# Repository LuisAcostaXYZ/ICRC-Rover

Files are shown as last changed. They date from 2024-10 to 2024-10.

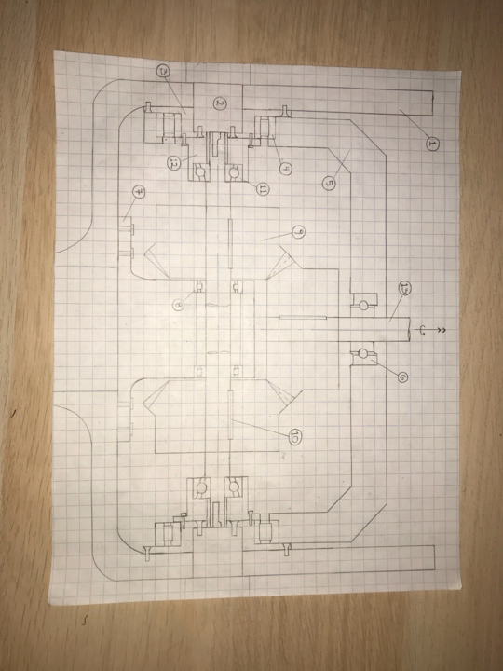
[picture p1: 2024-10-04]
3. ARM/3.0 2020-21 Arm/4. Robotic Arm/Robot 2.0 Design Files/Wrist/Wrist_2DSketch_v2.png

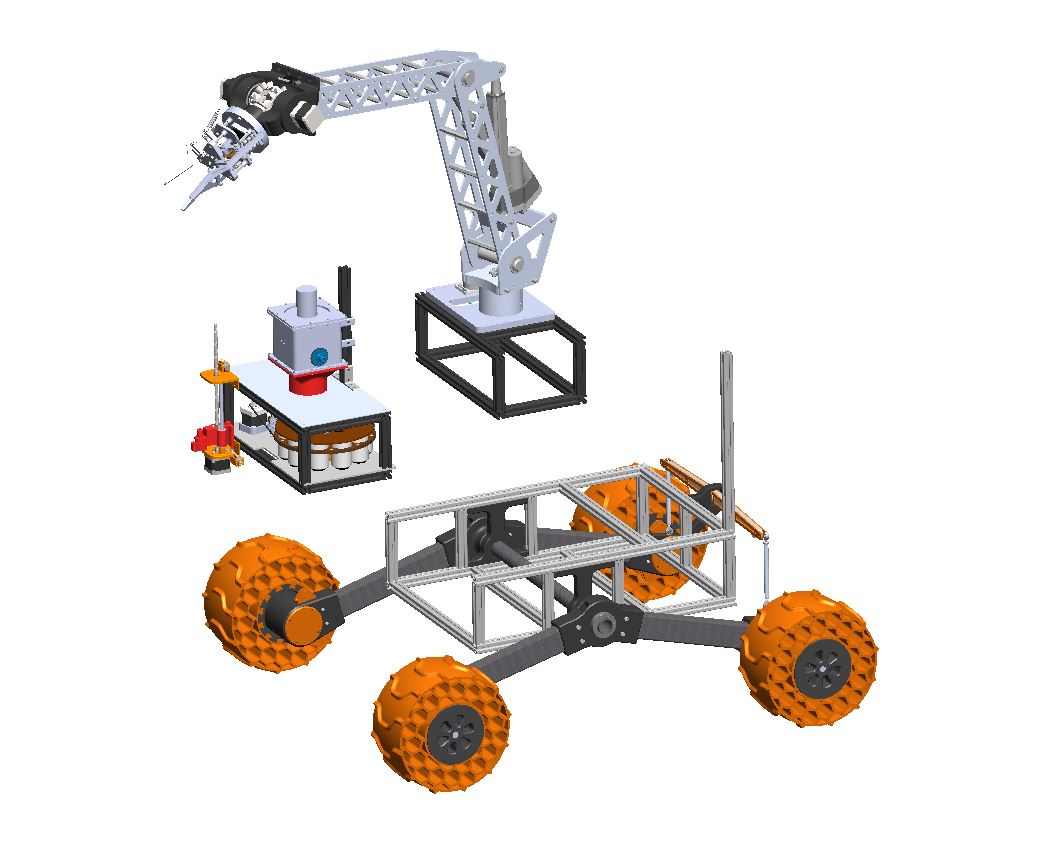
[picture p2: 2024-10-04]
Rover_thumbnail.JPG

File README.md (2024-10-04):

<h1>CIRC Rover</h1>

<h2>Description</h2>
The Canadian International Rover Challenge is a competition held every year in Drumheller, Alberta. This event brings together talented college and university STEM students from around the world. Here they have the chance to demonstrate their engineering abilities in robotic systems. The competition challenges the teams to design a space rover capable of overcoming difficult scenarios. These include traversing varying terrain, autonomous operations, and remote dexterity challenges using a robotic arm.
<br />

 ### [Video Demonstration](https://youtu.be/Zh-UuSO0Gxo?si=WTbHEEzv2XzP8nVz)
<p align="center">
UAV assembly
</p>

<h2>Software Used</h2>

- <b>SolidWorks</b> 

<h2>Directory structure:</h2>

The project is divided in 3 modules:  <br/>
- <b>1-CNC (Chassis and Suspension)</b>
- <b>2-LYF (Life Detection Dystem)</b>
- <b>3-ARM (Robotic arm)</b> <br/>

With an additional folder <b>"0-ROV"</b> containing the main assembly.

As the leader of the "Chassis and Suspension" division I supervised the progress the design, manufacturing and assembly of the models contained in the folder <b>“1-CNS”</b>.

<h2>ScreenShots:</h2>

<p align="center">
Chassis and suspension: <br/>
WingStructure
<br />
<br />
Wheel assembly:  <br/>
Wheel Assembly
<br />
<br />
Aluminium structure: <br/>
Aluminium structure
<br />

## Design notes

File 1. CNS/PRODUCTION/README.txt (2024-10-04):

All drawings and production documents are put here.

1. Create folder with the part number and name of the part/assembly that is entering production
2. Place pdf drawing and other production files (STEPs, STLs, DXFs...)
3. Notify appropriate lead for ordering the parts

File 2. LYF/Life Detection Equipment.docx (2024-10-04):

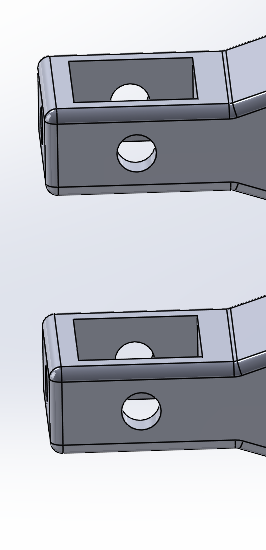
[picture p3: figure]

| Hole size? Add tolerance M4? 6 screws

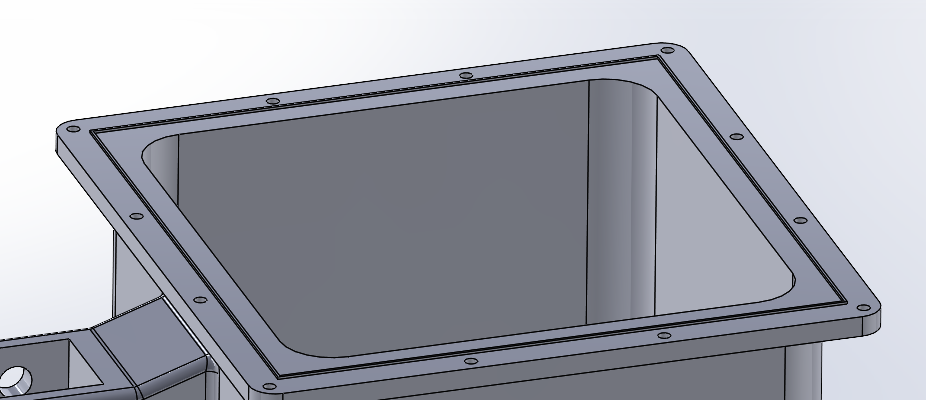
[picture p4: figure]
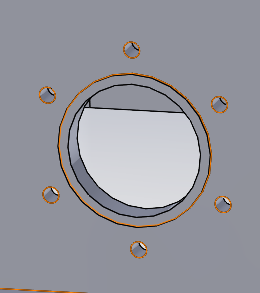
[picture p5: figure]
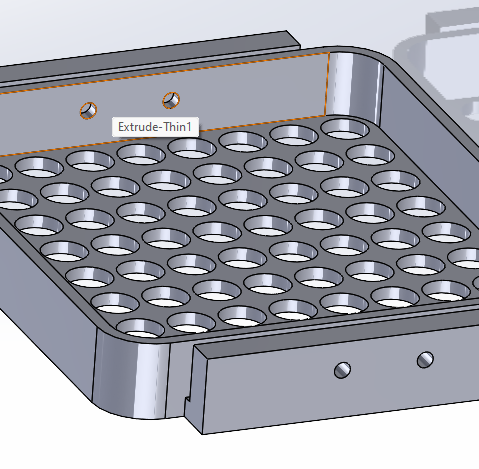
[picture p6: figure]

| M2 screws and nuts 12x2 >10 6 >9 4 >13

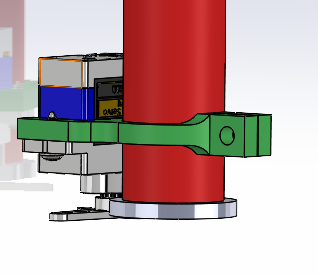
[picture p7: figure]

| M3 1>9 M2 2>7

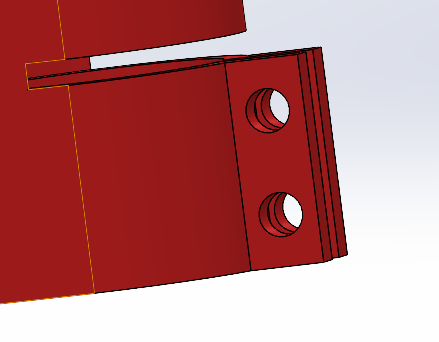
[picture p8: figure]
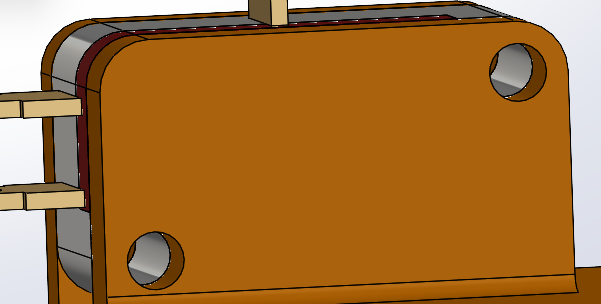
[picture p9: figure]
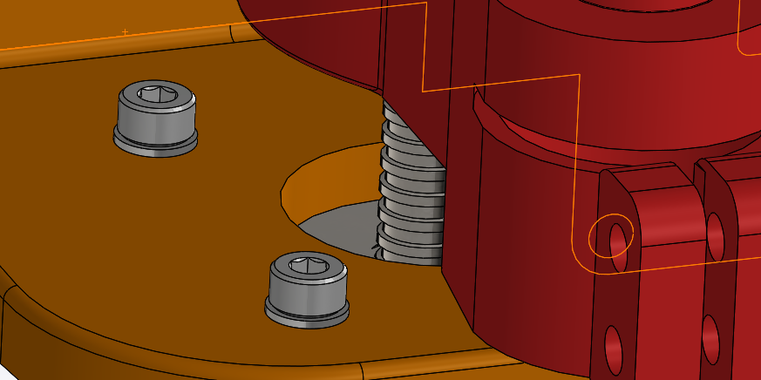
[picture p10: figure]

| M3 2>13 4>17 4 = 8mm
| M4 4

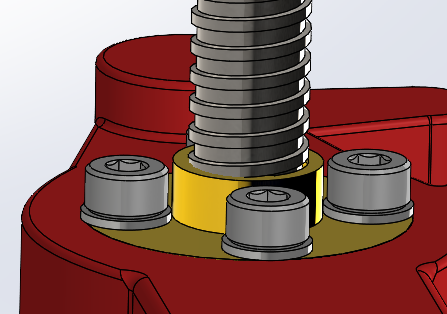
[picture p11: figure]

| 2 Bushings, 4 brass insert heat sinks, traveling nut M3 4=8mm

- Glue in vacuum?

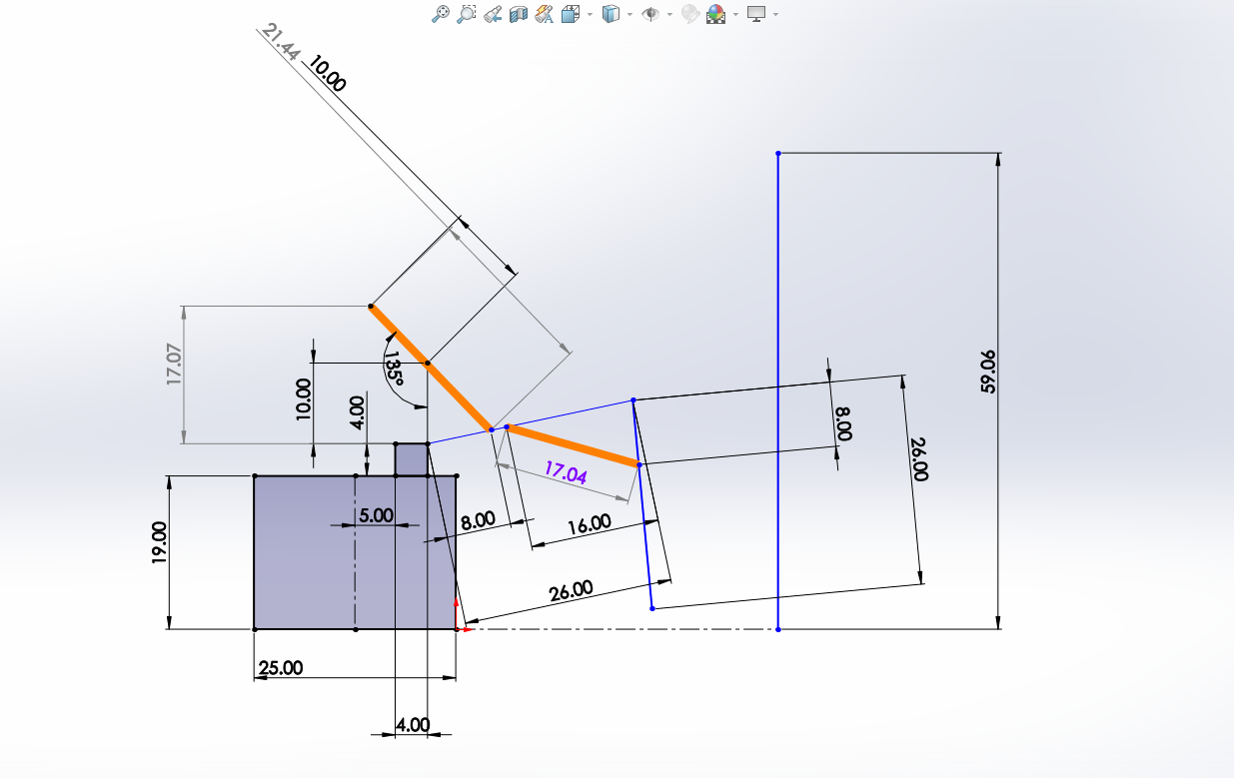
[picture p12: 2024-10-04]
3. ARM/3.0 2020-21 Arm/4. Robotic Arm/Robot 2.0 Design Files/Distance Diagram Robotic Arm V3.PNG

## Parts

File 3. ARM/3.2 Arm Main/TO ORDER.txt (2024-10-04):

McMaster Carr:
96640A362
90128A942
91290A140_Black-Oxide Alloy Steel Socket Head Screw
91780A082_Female Threaded Hex Standoff
91780A086_Female Threaded Hex Standoff
92375A410_Hairpin Cotter Pin
98410A133_External Retaining Ring
1327K68
1346K38
6389K627 P-005
6389K559 P-007

Firgelli Automations:
FA-OS-240-12-6

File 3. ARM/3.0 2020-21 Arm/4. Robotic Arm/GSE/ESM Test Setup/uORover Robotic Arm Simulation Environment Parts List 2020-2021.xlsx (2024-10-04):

 | uORover Robotic Arm Simulation Environment Parts List 2020-2021 |  |  |  | by Thomas Alkhoury
 |  |  |  |  | as of 09-09-2020
Item | Link | Price Per Unit (CAD) | Qty | Total Price (CAD)
Keyboard | https://www.amazon.ca/BlueDiamond-GDKB01-Connect-English-Keyboard/dp/B014P807Y6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 | 14.98 | 1 | 14.98
Button | https://www.digikey.ca/en/products/detail/adafruit-industries-llc/3488/7794999 | 3.79 | 3 | 11.37
Joystick | https://www.digikey.ca/en/products/detail/sparkfun-electronics/COM-09136/6596520 | 30.21 | 1 | 30.21
Toggle Switch | https://www.digikey.ca/en/products/detail/carling-technologies/DK284-73/483659?productid=483659 | 13.97 | 3 | 41.91
Turn Knob | https://www.digikey.ca/en/products/detail/nkk-switches/AT433A/1050352?productid=1050352 | 1.36 | 3 | 4.08
USB Port | https://www.digikey.ca/en/products/detail/bel-fuse-inc/0820-1X1T-00-F/9673514 | 5.3 | 1 | 5.3
Threaded Rod | https://www.mcmaster.com/98750A035/ | 1.71 | 1 | 1.71
Nut (Pack of 100) | https://www.mcmaster.com/95505a602 | 6.94 | 1 | 6.94
Raspberry Pi Zero W (Starter Kit) | https://www.amazon.ca/CanaKit-Raspberry-Wireless-Starter-Official/dp/B0727VRM14 | 73.13 | 1 | 73.13
Raspberry Pi Screen | https://www.amazon.ca/Kuman-Display-480x320-Raspberry-Interface/dp/B01CQIPEO0 | 24.99 | 1 | 24.99
Joystick Screw (Pack of 100) | https://www.mcmaster.com/90031A223/ | 6.04 | 1 | 6.04
Keyboard Door Latch | https://www.homedepot.ca/product/richelieu-stainless-steel-heavy-duty-chest-latch/1000508751 | 8.98 | 1 | 8.98
Toggle Switch Cover | https://www.digikey.com/product-detail/en/cw-industries/GT-4R/CWI312-ND/3587645 | 3.63 | 3 | 10.89
Potentiometer | https://www.digikey.ca/en/products/detail/tt-electronics-bi/P164M211FNA25D103/12162405 | 2.55 | 3 | 7.65
Drawer Wheels And Mount | https://www.homedepot.ca/product/everbilt-1-1-2-inch-soft-rubber-wheel-rigid-caster-with-40-lb-load-rating/1000404245 | 3.03 | 2 | 6.06
Frame L Bracket | https://www.homedepot.ca/product/everbilt-1-1-2-inch-zinc-corner-brace-4-pack-/1000773638 | 1.85 | 4 | 7.4
Drawer Wheel Mount Screw (Pack of 100) | https://www.mcmaster.com/90031A108/ | 2.68 | 1 | 2.68
Keyboard Door Hinge | https://www.homedepot.ca/product/blum-full-overlay-clip-hinge-with-plate-100-degree/1000106078 | 12.73 | 1 | 12.73
 |  |  | TOTAL | 277.05

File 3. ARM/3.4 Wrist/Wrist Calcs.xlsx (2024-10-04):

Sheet: Loading Cases on Bushings
Constants | Mass [kg] | Weight [N]
EE | 1.063 | 10.63
Payload | 5 | 50 | URC
Astronaut | 60 | 600 | CIRC
Loads on Bushings
Loading Case | Bushing | Axial Load [N] | Radial Load [N] | S.F | Rated Axial Load [N] | Rated Radial Load [N]
Horizontal | Front | 0 | 610.63 | 1.5 | 0 | 915.945
 | Side | 0 | 305.315 |  | 0 | 457.9725
Vertical | Front | 610.63 | 0 |  | 915.945 | 0 | In vertical case, we would carry 5kg payload
 | Side | 0 | 305.315 |  | 0 | 457.9725 | In horizontal case, we could carry 5kg payload or drag an astronaut
Max Loads
Bushing | Axial Load [N] | Radial [N] |  |  | `
Front | 915.945 | 915.945
Side | 0 | 457.9725
Note: Axial load on front bushing will be counter-acted by 3D print
 | 90.945N= | 20.289007 lbf
 | 45.4725N= | 10.2225123 lbf

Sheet: Bushing Selection
Bushing | Description | Dynamic Radial Load Capacity [lbs] | RPM | Source | Cost | Machining Req'd.
Front | Ultra-Low-Friction Oil-Embedded Sleeve Bearing for 14 mm Shaft Diameter, for 20 mm Housing ID, 22 mm Long |  |  | https://www.mcmaster.com/1688K162/ |  | N/A
Side | Oil-Embedded 841 Bronze Sleeve Bearing for 50 mm Shaft Diameter and 60 mm Housing ID, 50 mm Long |  |  | https://www.mcmaster.com/6658K774/ |  | Lathe (parting)
Side | Light Duty Dry-Running Nylon Sleeve Bearing for 50 mm Shaft Diameter, for 60 mm Housing ID, 50 mm Long | 620 | 30 | https://www.mcmaster.com/6389K955/ |  | Lathe (parting)

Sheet: Output Shaft
Arm Configuration | Horizontal | Vertical
Loading Case
5 kg payload
horizontal case

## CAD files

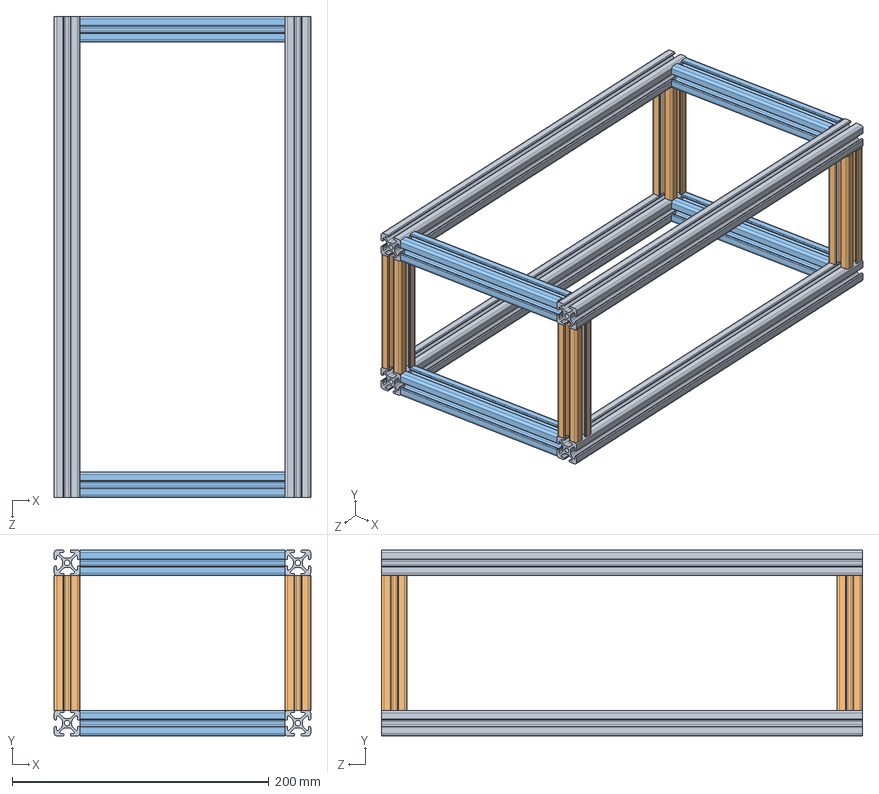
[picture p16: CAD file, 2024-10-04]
2. LYF/1. Life detection module/UOR23-LYF-1-A-001.SLDASM
200.0 x 145.0 x 375.0 mm
UOR23-LYF-1-P-001 x 4
UOR23-LYF-1-P-002 x 4
UOR23-LYF-1-P-003 x 4

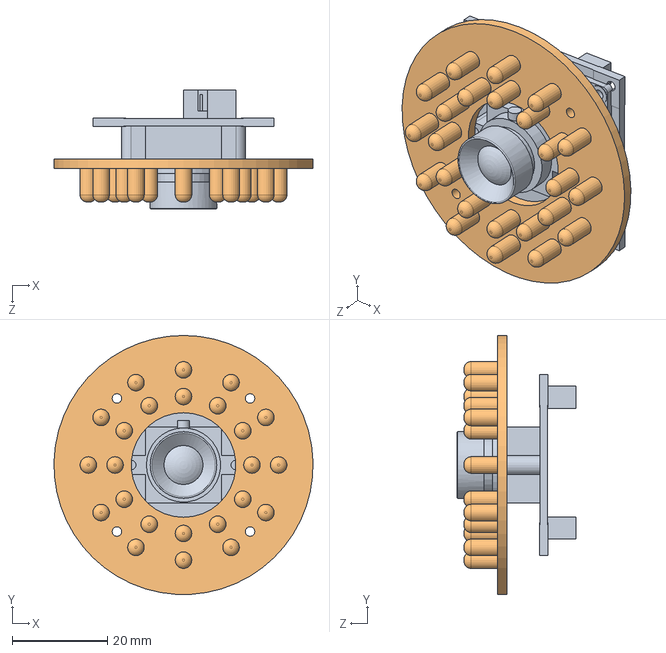
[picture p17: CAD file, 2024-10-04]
2. LYF/4. Rotary Sample System/Camera assembly/ELP-USB-720p camera assy.SLDASM
54.5 x 54.5 x 25.1 mm
elp-usb500w05g-fd100
LED Ring

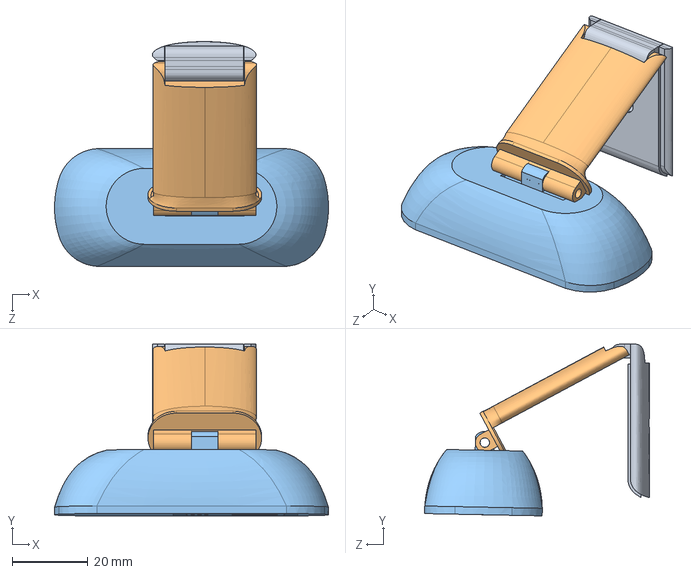
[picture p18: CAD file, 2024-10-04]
2. LYF/4. Rotary Sample System/Logitech C270/logitech_webcam_c270.SLDASM
72.2 x 45.3 x 59.3 mm
mount_bottom
logitech_webcam_c270

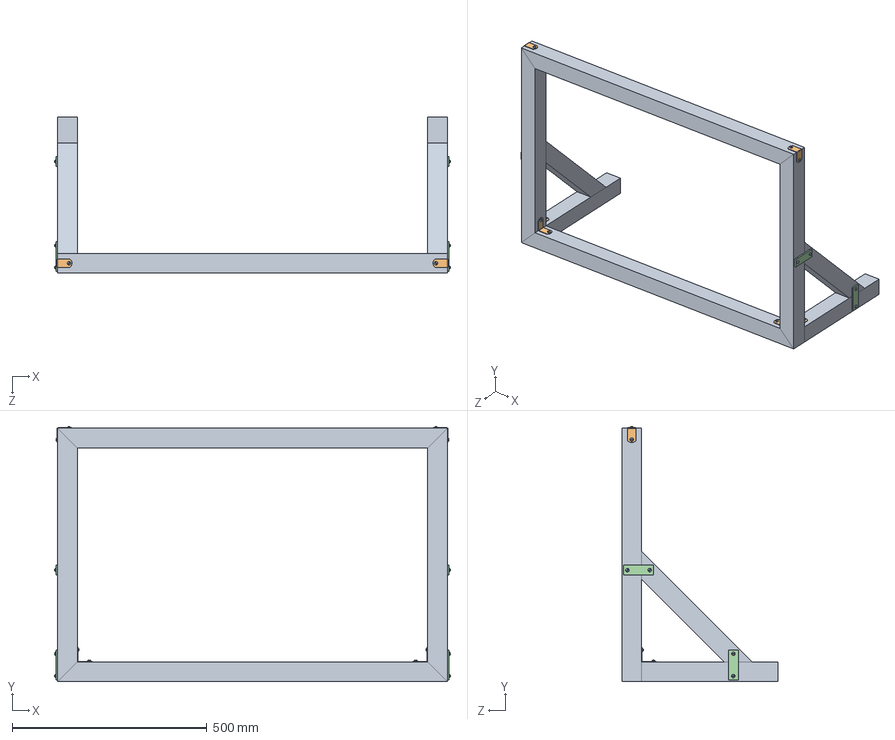
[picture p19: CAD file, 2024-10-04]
3. ARM/3.0 2020-21 Arm/4. Robotic Arm/GSE/ESM Test Setup/Lumbar Support.SLDASM
1016.0 x 654.7 x 400.8 mm
Lumbar supports x 8
15705A450_BRACKET x 6
92407A245_BRASS SLOTTED DECORATIVE ROUNDED HEAD SCREWS x 19
1030A400_BRACKET x 4
Mirror92407A245_BRASS SLOTTED DECORATIVE ROUNDED HEAD SCREWS

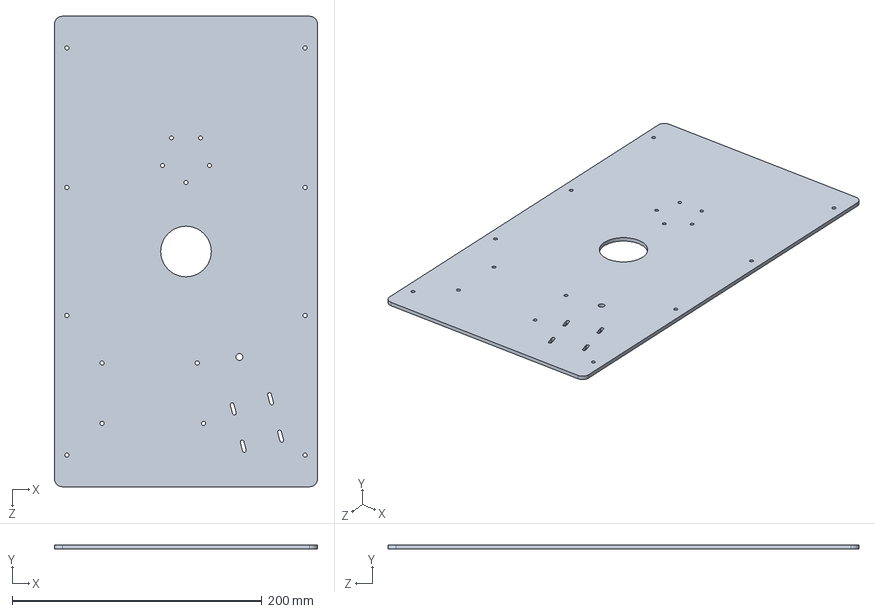
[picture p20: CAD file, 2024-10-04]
3. ARM/3.0 2020-21 Arm/4. Robotic Arm/Mounts for Electrical Enclosure/baseplate full.SLDPRT
210.6 x 3.30 x 376.8 mm

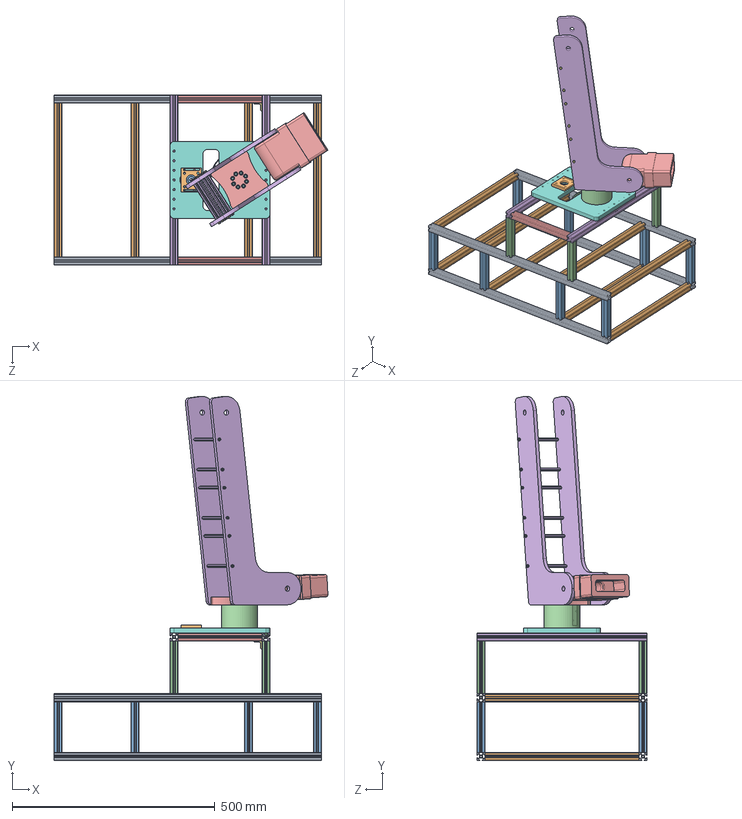
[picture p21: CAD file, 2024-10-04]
3. ARM/3.0 2020-21 Arm/4. Robotic Arm/Robot 2.0 Design Files/Chassis and Mounting Frame Assembly.SLDASM
676.0 x 898.5 x 420.1 mm
8020-460mm^UOM20-A-10001 x 4
8020-380.020400mm^UOM20-A-10001 x 8
8020-Vertical^UOM20-A-10001 x 8
Vertical Beam x 4
Top parallel horontal Beam 250mm x 2
Top horontal Beam x 2
5537T935_ALUMINUM T-SLOTTED FRAMING EXTRUSION (20mm) x 2
BasePlate
Pulley 60T
J1 Spindle
Bearing 32009X x 2
J1 Turret Housing
J1 Turret Platform
SupportArm x 2
93070A101_LOW-PROFILE SOCKET HEAD CAP SCREW x 8
96144A116_METRIC CLASS 12.9 SOCKET HEAD CAP SCREW x 8
92605A115_NONMARRING FLAT POINT SET SCREW x 4
J1 & J3 Motor Mount
Pulley 15T
6484K228_TIMING BELT
Base Male Connector
91115A843_18-8 SS FEM THRDED HEX STANDOFF x 6
92196A196_18-8 STAINLESS STEEL SOCKET HEAD SCREW x 12

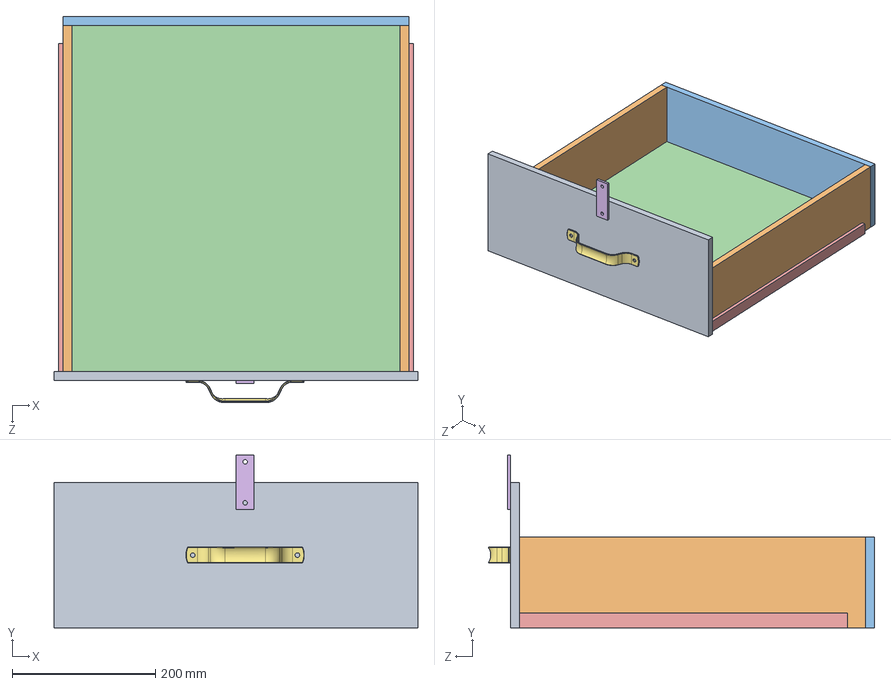
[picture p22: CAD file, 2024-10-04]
3. ARM/3.5 Testing Rig/Production/UOR23-ARM-5-A-001-Drawer.SLDASM
508.0 x 241.3 x 539.0 mm
UOR23-ARM-5-P-013-Drawer_Front
UOR23-ARM-5-P-011-Drawer_Side x 2
UOR23-ARM-5-P-012-Drawer Back
UOR23-ARM-5-P-014-Drawer_Bottom
UOR23-ARM-5-P-015-Drawer_Slides x 2
1030A4_Flat-Surface Bracket
5185A1_Unthreaded-Hole Rectangular Pull Handle

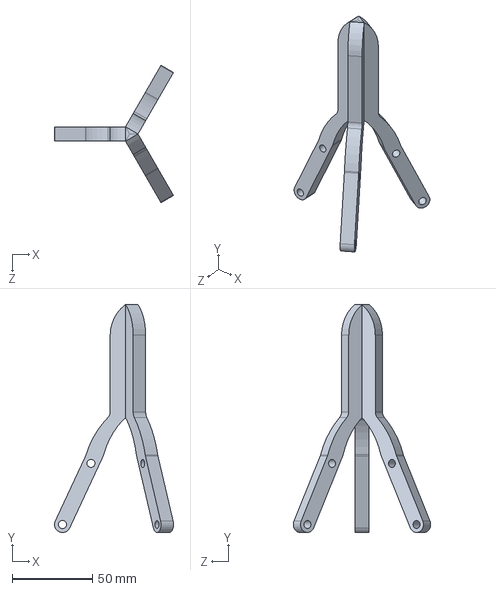
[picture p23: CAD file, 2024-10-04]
3. ARM/Tst/Assem1.SLDASM
74.1 x 142.0 x 85.6 mm
Talon V2 x 3

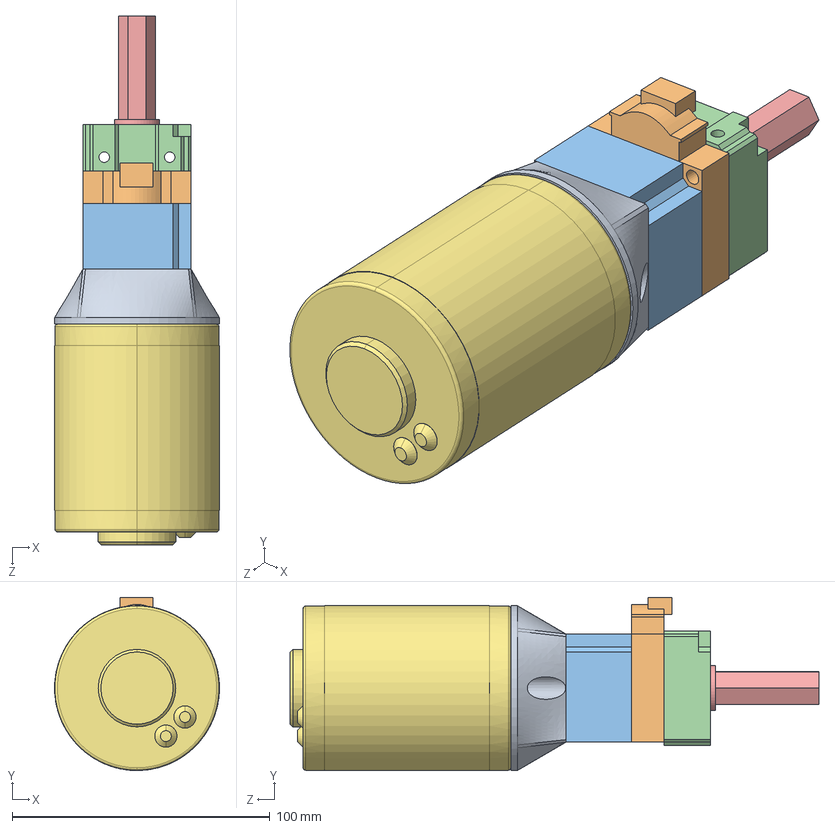
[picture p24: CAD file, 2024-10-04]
1. CNS/Sandbox/Send to Ze Feb 2/CIM motor assembled with encoder.SLDASM
64.0 x 67.2 x 205.1 mm
CIM adapter
Integrated encoder
Gearbox mid section
Planetary gearbox attachement to wheel
Hex shaft
Hex shaft base
CIM mini motor

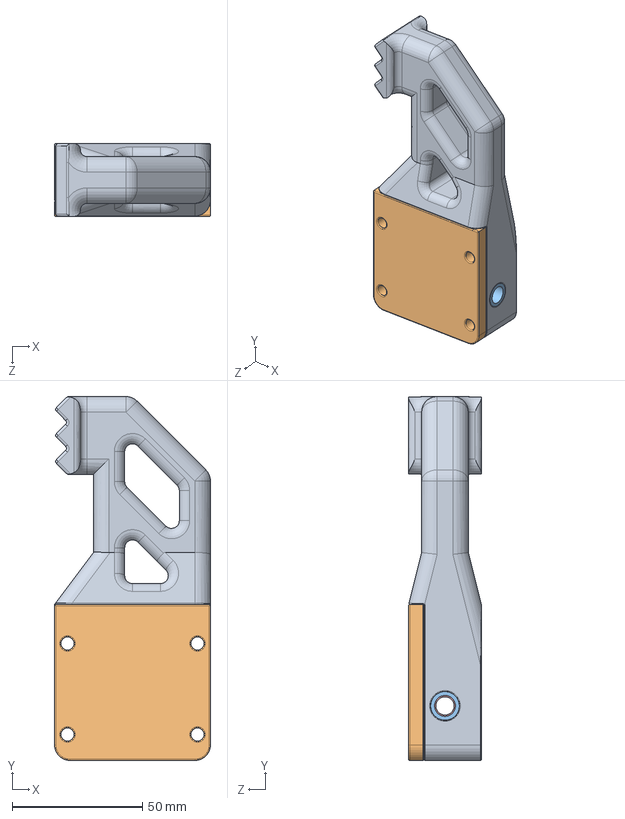
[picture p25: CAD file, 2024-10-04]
3. ARM/3.0 2020-21 Arm/4. Robotic Arm/Robot 2.0 Design Files/Endeffector V2/final effector/UOM20-4A006.SLDASM
60.0 x 140.0 x 28.0 mm
UOM20-4P011
UOM20-4P036
6659K676_OIL-EMBEDDED FLANGED SLEEVE BEARING x 2
9434K135_MUSIC-WIRE STEEL COMPRESSION SPRINGS
leadnut
UOM20-4P038

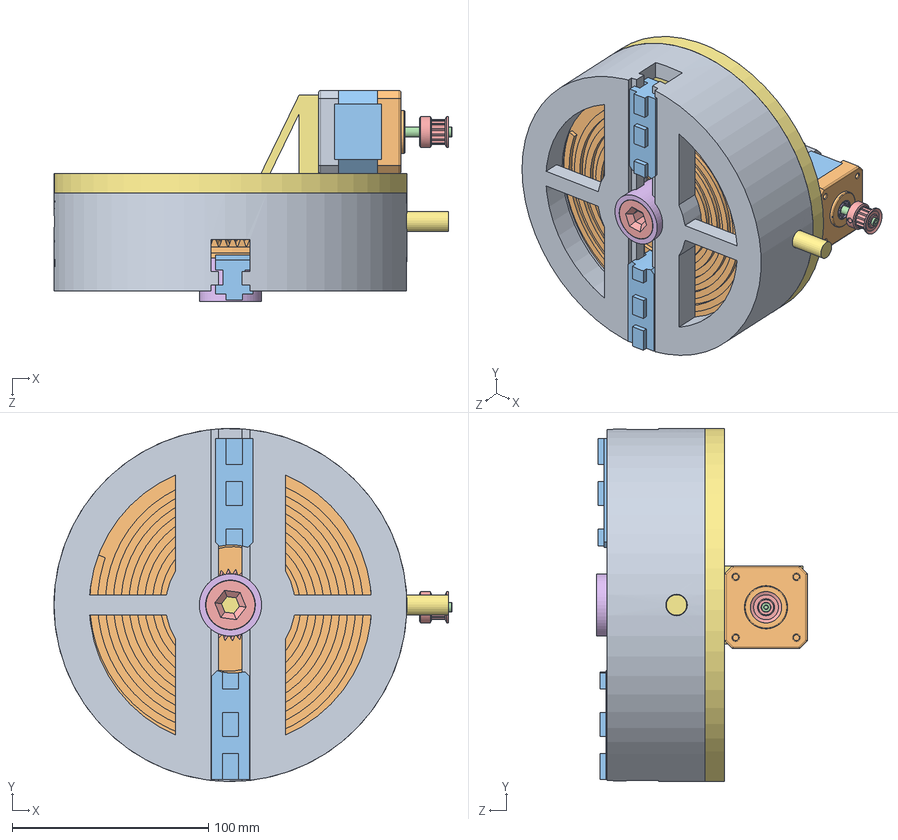
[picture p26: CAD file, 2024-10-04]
3. ARM/3.0 2020-21 Arm/4. Robotic Arm/Robot 2.0/End Effecter/V1/Assem1.SLDASM
203.0 x 180.1 x 107.6 mm
frame
threaded plate
linear block x 2
30204-rollers
shaft
needle bearing
cover
30204-base
BASE
BACK PLATE
AXIAL ROD
PULLEY
instrument ball bearing_68_am x 2
screw

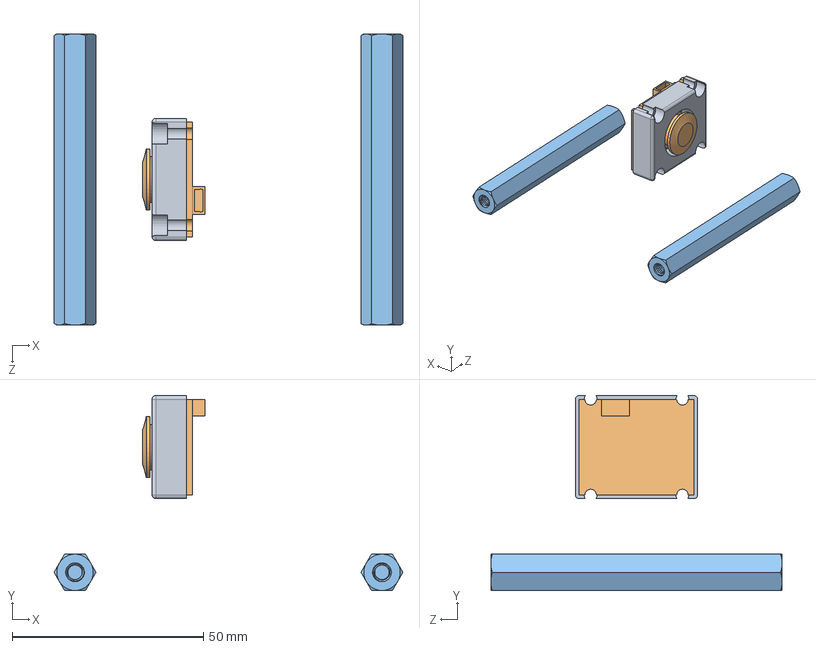
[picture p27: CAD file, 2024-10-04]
3. ARM/3.6 Camera Mount (Elbow)/Rover_Mount_Base.SLDASM
91.3 x 51.0 x 76.2 mm
UOR23-ARM-1-P-008-Camera_Cover
UOR23-ARM-1-P-010-Camera
91780A082_Female Threaded Hex Standoff x 2

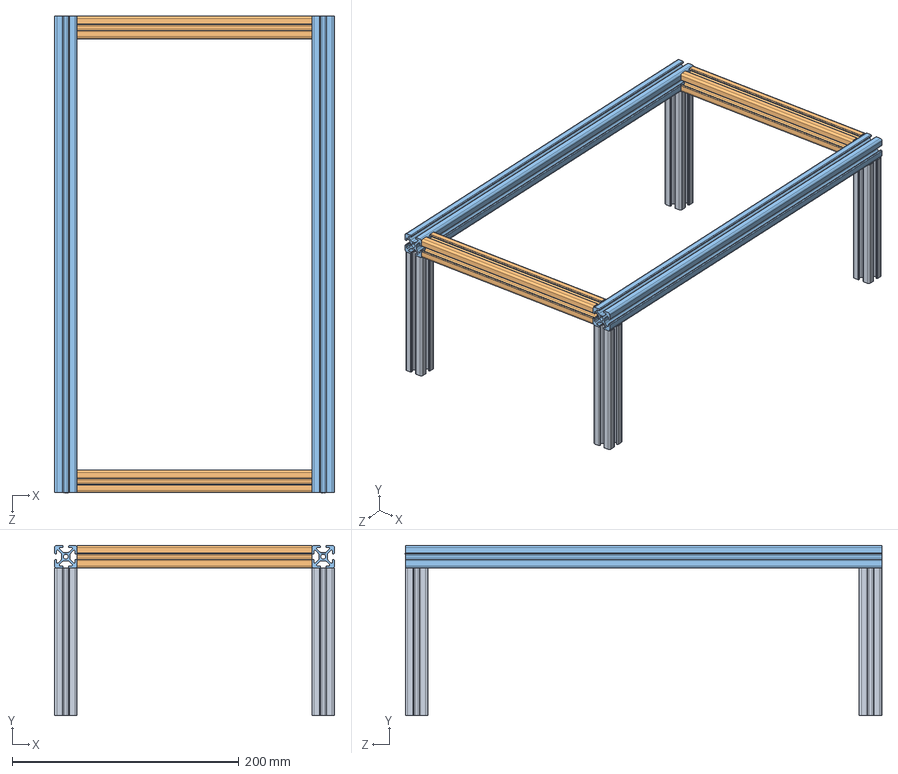
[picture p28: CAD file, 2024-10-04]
3. ARM/3.0 2020-21 Arm/4. Robotic Arm/Robot 2.0 Design Files/Chassis Platform/Mounting Frame.SLDASM
246.8 x 150.1 x 420.1 mm
Vertical Beam x 4
Top parallel horontal Beam 250mm x 2
Top horontal Beam x 2

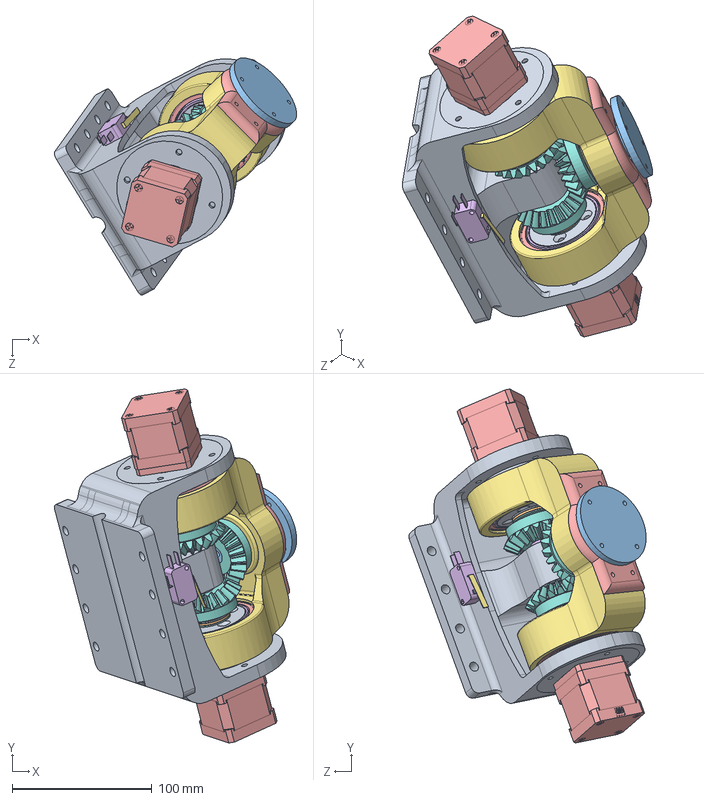
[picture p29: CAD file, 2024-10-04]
3. ARM/3.0 2020-21 Arm/4. Robotic Arm/Robot 2.0 Design Files/Wrist/UOM20-4A004.SLDASM
173.2 x 253.2 x 169.7 mm
Motor sleeve x 2
HK_1412_3 x 32
HK_1412_20 x 32
HK_1412_37 x 2
17HS15-1684D-HG10-AR3 x 2
shaft x 2
AXK_1528___AS_1528___AS_1528_3 x 40
AXK_1528___AS_1528___AS_1528_24 x 2
AXK_1528___AS_1528___AS_1528_26 x 2
AXK_1528___AS_1528___AS_1528_28 x 2
2mm spacer x 2
NKI_50_25_37 x 66
NKI_50_25_71 x 2
NKI_50_25_73 x 2
Wrist output frame
7203_BEY_3 x 20
7203_BEY_14 x 2
7203_BEY_16 x 2
Output shaft
4mm spacer
Wrist output cap
V_152_1C25_BASE x 2
V_152_1C25_ACTUATOR x 2
straight miter gear_am x 3
Wrist input frame_attachment

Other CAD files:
3. ARM/3.0 2020-21 Arm/4. Robotic Arm/Robot 2.0 Design Files/Wrist/v4/HK_1412.sldasm
3. ARM/3.4 Wrist/3.4.1 Wrist 1.0/V_152_1C25.SLDASM
3. ARM/3.4 Wrist/3.4.2 Wrist 1.5/Sandbox/V_152_1C25.SLDASM
3. ARM/3.4 Wrist/3.4.1 Wrist 1.0/AXK_2035___AS_2035___AS_2035.sldasm
1. CNS/1. Chassis/Drawings/UOR23-CNS-1-P-005-I_Piece_Support.SLDDRW
1. CNS/1. Chassis/Drawings/UOR23-CNS-1-P008_SidePlate.SLDDRW
1. CNS/1. Chassis/Drawings/UOR23-CNS-1-P009_Back_Panel.SLDDRW
1. CNS/1. Chassis/Drawings/UOR23-CNS-1-P010-bottomPanel.SLDDRW
1. CNS/1. Chassis/UOR23-CNS-1-A-001_Chassis_assembly.SLDASM
1. CNS/1. Chassis/UOR23-CNS-1-A-001_Chassis_assembly.SLDDRW
1. CNS/1. Chassis/UOR23-CNS-1-P-001_80-20_frame_element_mid.SLDPRT
1. CNS/1. Chassis/UOR23-CNS-1-P-002_80-20_frame_element_long.SLDPRT
1. CNS/1. Chassis/UOR23-CNS-1-P-003_80-20_frame_element_short.SLDPRT
1. CNS/1. Chassis/UOR23-CNS-1-P-004_Mast.SLDPRT
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

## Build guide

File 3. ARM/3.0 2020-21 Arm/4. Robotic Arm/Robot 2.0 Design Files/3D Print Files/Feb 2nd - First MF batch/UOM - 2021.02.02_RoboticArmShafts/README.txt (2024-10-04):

****************************************************
*  Robotic Arm print files  *  Date: Feb 2nd 2021  *  
****************************************************

Please print the following items on the MarkForge II with Onyx filament.

shaft.STL, quantity 2
 - orientate shaft with female coupling facing up
 - 100% infill, while maximizing the number of wall lines
 - Place items closer together and potentially use a raft setting for better build plate adhesion. 

Output shaft.STL, quantity 1
 - orientate shaft with the flange face down
 - 100% infill, while maximizing the number of wall lines

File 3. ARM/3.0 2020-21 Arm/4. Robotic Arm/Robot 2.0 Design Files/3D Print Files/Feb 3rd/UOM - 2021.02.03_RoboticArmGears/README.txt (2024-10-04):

****************************************************
*  Robotic Arm print files  *  Date: Feb 2nd 2021  *  
****************************************************

Please print the following items on the MarkForge II with Onyx filament.

A 1C 4MYKW25020_15mm bore.STL, quantity 2

A 1C 4MYKW25020_15mm bore_modified.STL, quantity 1

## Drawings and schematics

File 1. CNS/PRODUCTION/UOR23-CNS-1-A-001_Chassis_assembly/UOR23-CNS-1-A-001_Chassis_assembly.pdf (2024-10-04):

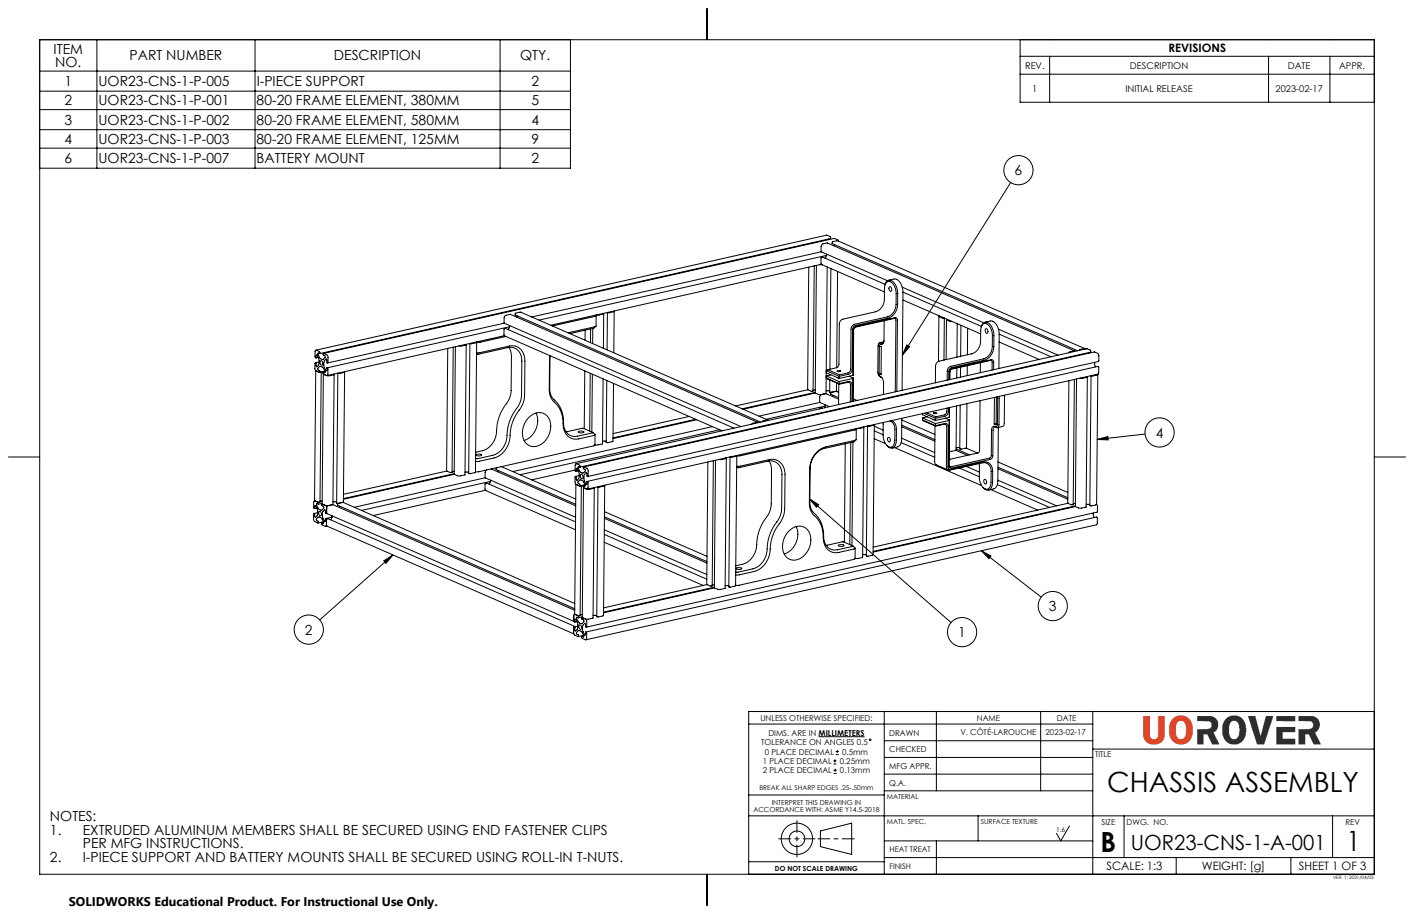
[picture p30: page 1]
PART NUMBER; DESCRIPTION; QTY.; SHEET 1 OF 3; SCALE: 1:3; WEIGHT: [g]; DWG. NO.; REV; MFG APPR.; V. CÔTÉ-LAROUCHE; HEAT TREAT; MATL. SPEC.; SURFACE TEXTURE; CHASSIS ASSEMBLY; VER. 1: 2021/04/03

REV. | DESCRIPTION | DATE | APPR.
1 | INITIAL RELEASE | 2023-02-17

1 | UOR23-CNS-1-P-005 | I-PIECE SUPPORT | 2
2 | UOR23-CNS-1-P-001 | 80-20 FRAME ELEMENT, 380MM | 5
3 | UOR23-CNS-1-P-002 | 80-20 FRAME ELEMENT, 580MM | 4
4 | UOR23-CNS-1-P-003 | 80-20 FRAME ELEMENT, 125MM | 9
6 | UOR23-CNS-1-P-007 | BATTERY MOUNT | 2

UNLESS OTHERWISE SPECIFIED:
DIMS. ARE IN MILLIMETERS
TOLERANCE ON ANGLES 0.5
0 PLACE DECIMAL 0.5mm
1 PLACE DECIMAL 0.25mm
2 PLACE DECIMAL 0.13mm

BREAK ALL SHARP EDGES .25-.50mm
MATERIAL INTERPRET THIS DRAWING IN
ACCORDANCE WITH: ASME Y14.5-2018

NOTES:
1. EXTRUDED ALUMINUM MEMBERS SHALL BE SECURED USING END FASTENER CLIPS
PER MFG INSTRUCTIONS.
2. I-PIECE SUPPORT AND BATTERY MOUNTS SHALL BE SECURED USING ROLL-IN T-NUTS.

DO NOT SCALE DRAWING

SOLIDWORKS Educational Product. For Instructional Use Only.

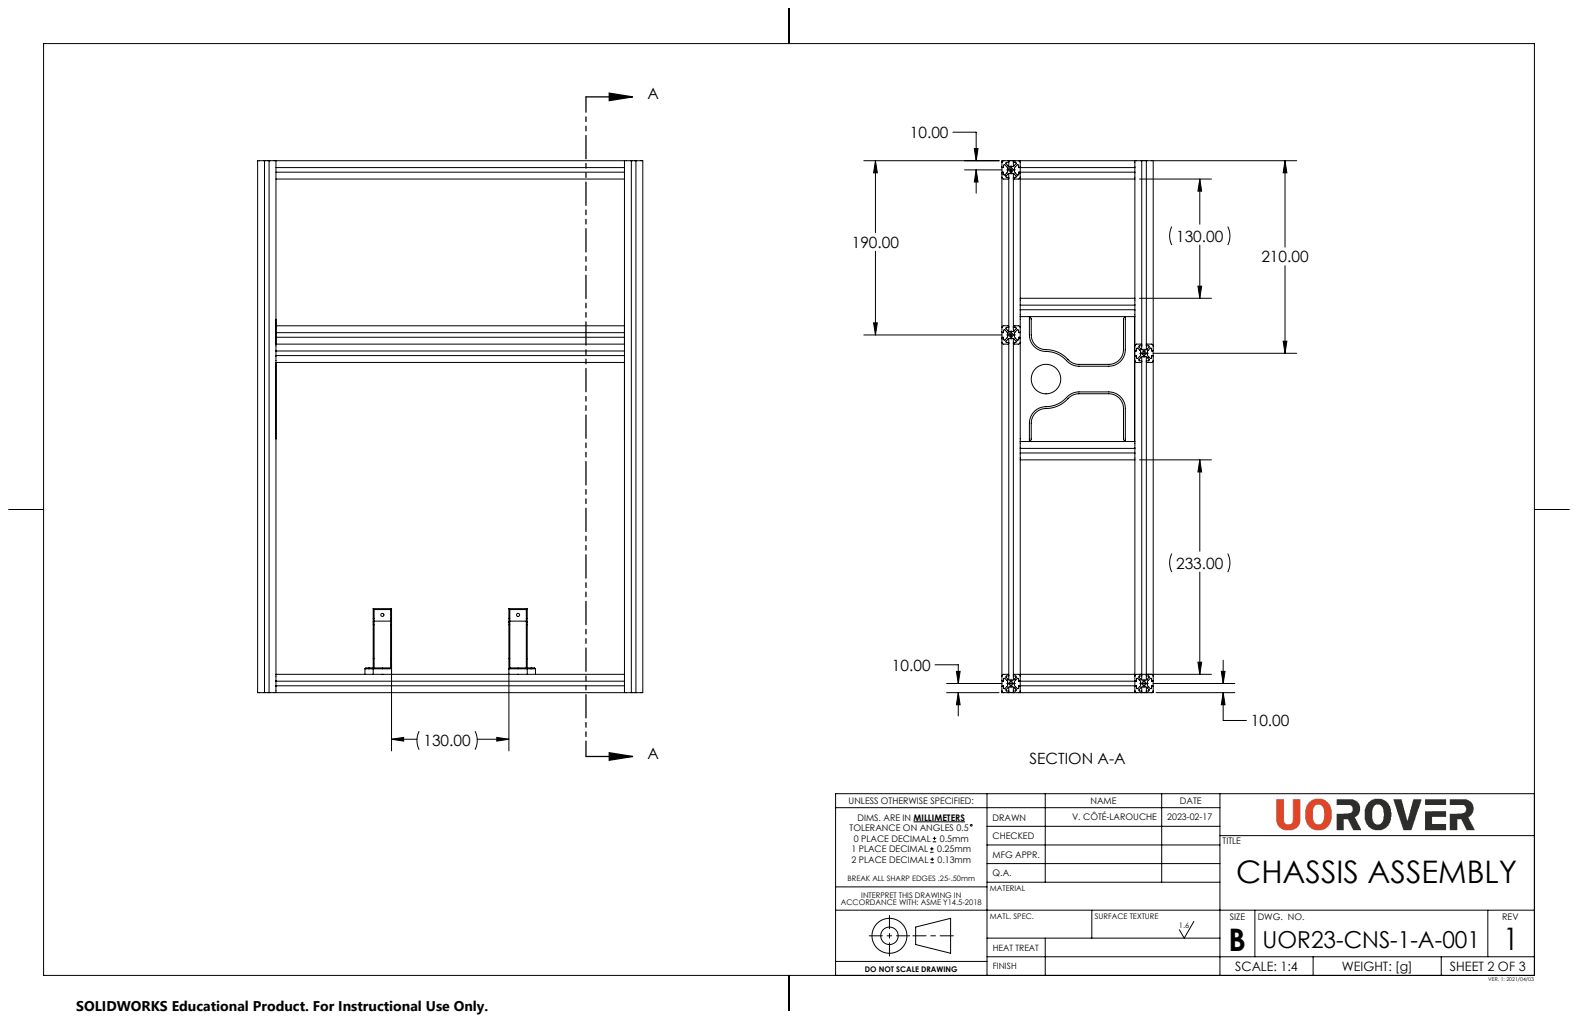
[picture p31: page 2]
SECTION A-A; SCALE: 1:4; WEIGHT: [g]; DWG. NO.; REV; MFG APPR.; V. CÔTÉ-LAROUCHE; MATL. SPEC.; SURFACE TEXTURE; CHASSIS ASSEMBLY

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

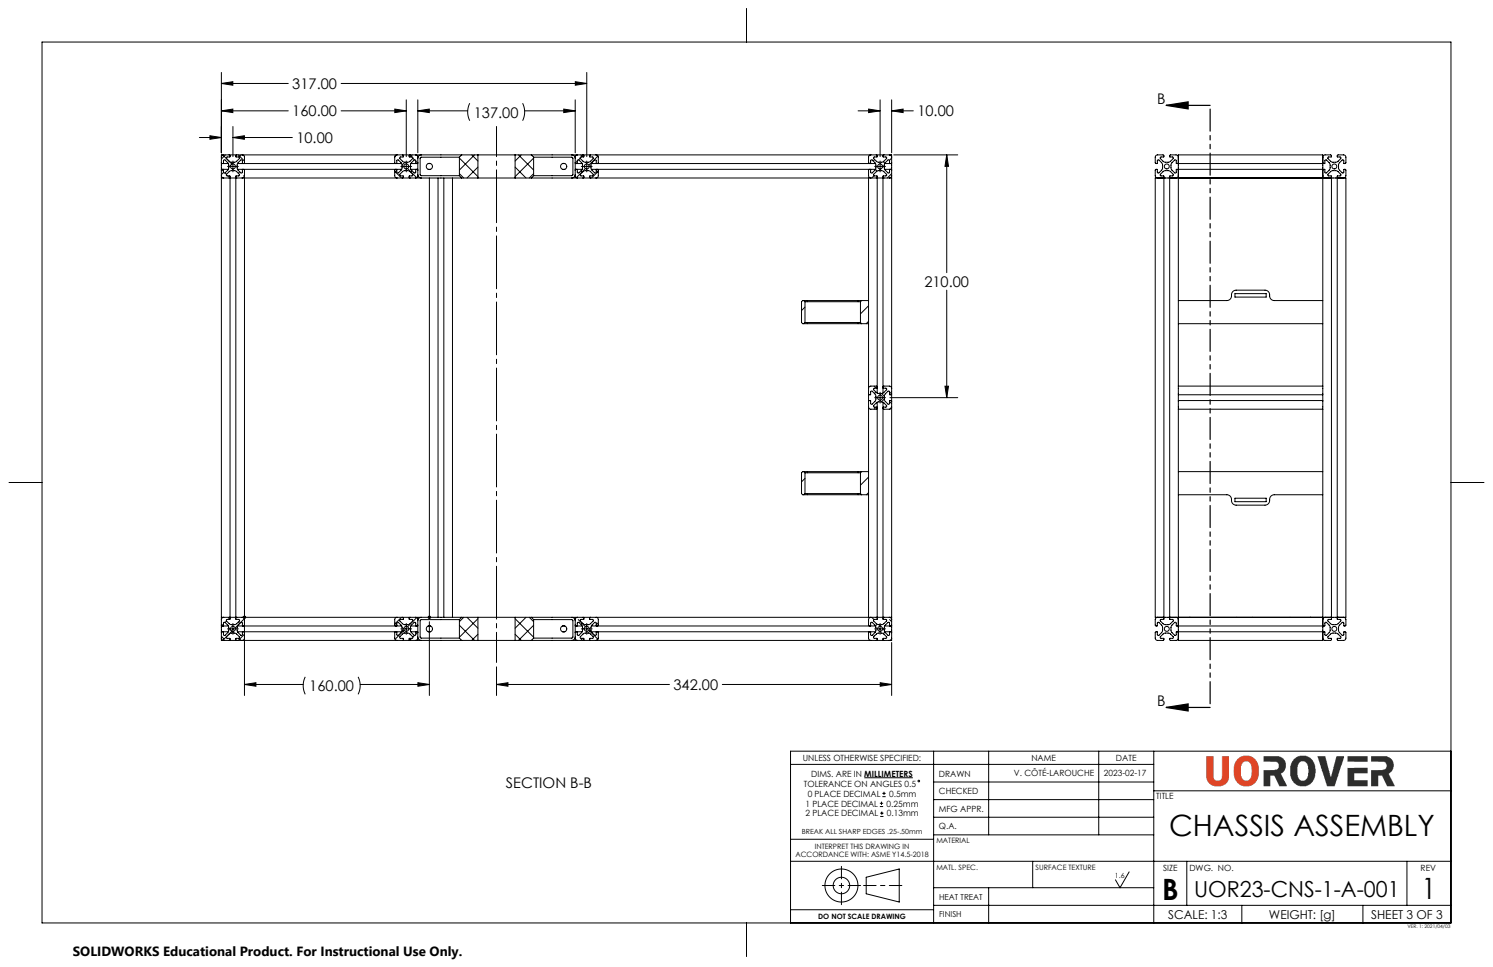
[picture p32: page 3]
SECTION B-B; SCALE: 1:3; WEIGHT: [g]; DWG. NO.; REV; MFG APPR.; V. CÔTÉ-LAROUCHE; MATL. SPEC.; SURFACE TEXTURE; CHASSIS ASSEMBLY

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

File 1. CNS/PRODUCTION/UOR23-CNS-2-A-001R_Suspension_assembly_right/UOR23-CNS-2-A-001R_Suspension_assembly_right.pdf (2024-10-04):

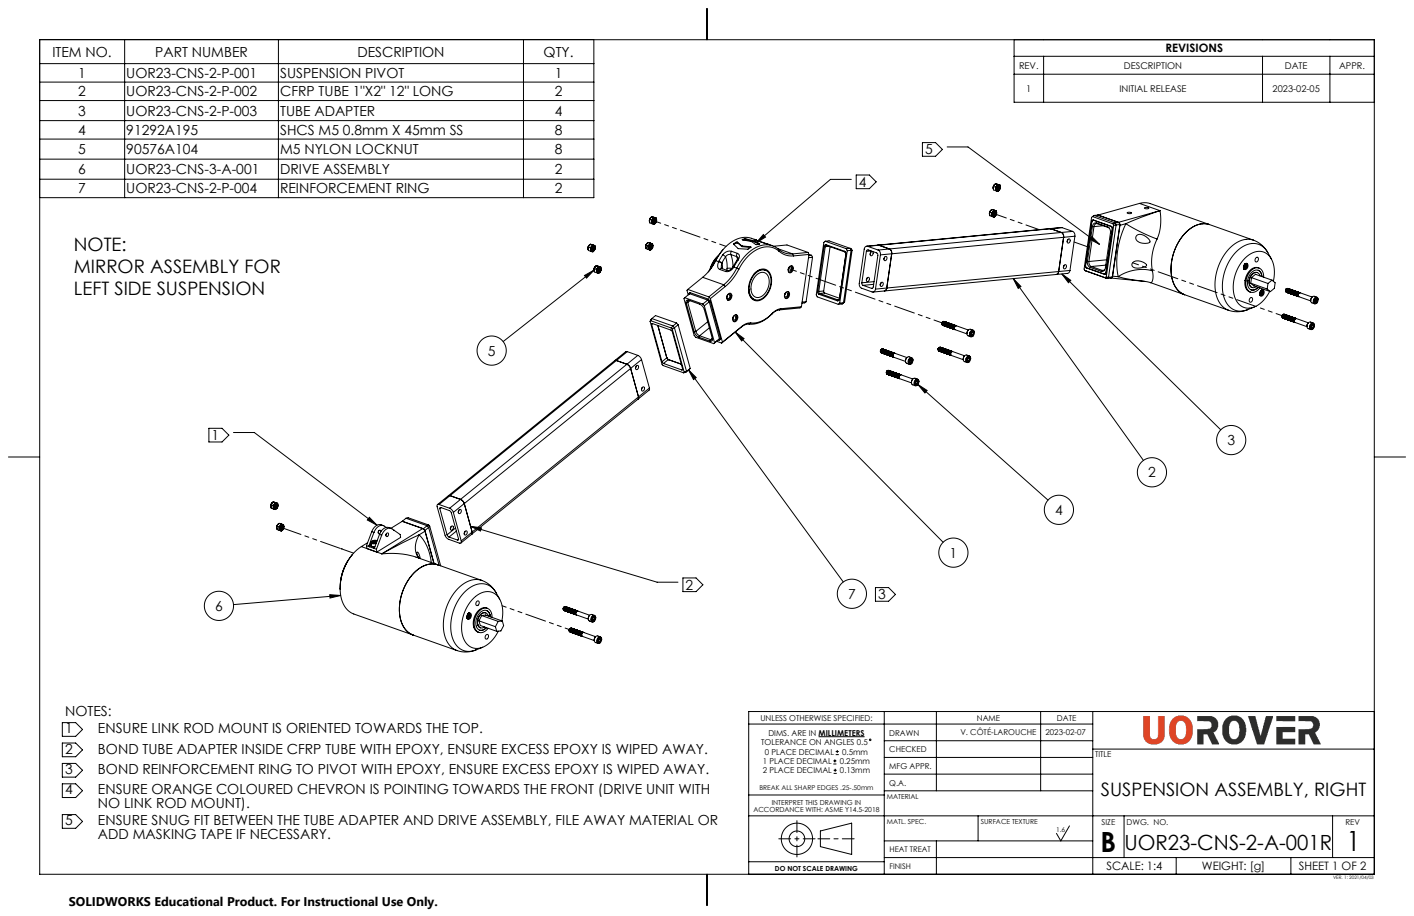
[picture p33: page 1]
ENSURE LINK ROD MOUNT IS ORIENTED TOWARDS THE TOP.; BOND TUBE ADAPTER INSIDE CFRP TUBE WITH EPOXY, ENSURE EXCESS EPOXY IS WIPED AWAY.; BOND REINFORCEMENT RING TO PIVOT WITH EPOXY, ENSURE EXCESS EPOXY IS WIPED AWAY.; ENSURE ORANGE COLOURED CHEVRON IS POINTING TOWARDS THE FRONT (DRIVE UNIT WITH; ENSURE SNUG FIT BETWEEN THE TUBE ADAPTER AND DRIVE ASSEMBLY, FILE AWAY MATERIAL OR; ITEM NO.; PART NUMBER; DESCRIPTION; QTY.; SHEET 1 OF 2; SCALE: 1:4; WEIGHT: [g]; DWG. NO.; REV; V. CÔTÉ-LAROUCHE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

1 | UOR23-CNS-2-P-001 | SUSPENSION PIVOT | 1
2 | UOR23-CNS-2-P-002 | CFRP TUBE 1"X2" 12" LONG | 2
3 | UOR23-CNS-2-P-003 | TUBE ADAPTER | 4
4 | 91292A195 | SHCS M5 0.8mm X 45mm SS | 8
5 | 90576A104 | M5 NYLON LOCKNUT | 8
6 | UOR23-CNS-3-A-001 | DRIVE ASSEMBLY | 2
7 | UOR23-CNS-2-P-004 | REINFORCEMENT RING | 2

REV. | DESCRIPTION | DATE | APPR.
1 | INITIAL RELEASE | 2023-02-05

NOTE:
MIRROR ASSEMBLY FOR
LEFT SIDE SUSPENSION

NOTES:
NO LINK ROD MOUNT).
ADD MASKING TAPE IF NECESSARY.

UNLESS OTHERWISE SPECIFIED:
DIMS. ARE IN MILLIMETERS
TOLERANCE ON ANGLES 0.5
0 PLACE DECIMAL 0.5mm
1 PLACE DECIMAL 0.25mm
2 PLACE DECIMAL 0.13mm

DRAWN
CHECKED
MFG APPR.
SUSPENSION ASSEMBLY, RIGHT Q.A.

BREAK ALL SHARP EDGES .25-.50mm
MATERIAL INTERPRET THIS DRAWING IN
ACCORDANCE WITH: ASME Y14.5-2018

DO NOT SCALE DRAWING

SOLIDWORKS Educational Product. For Instructional Use Only.

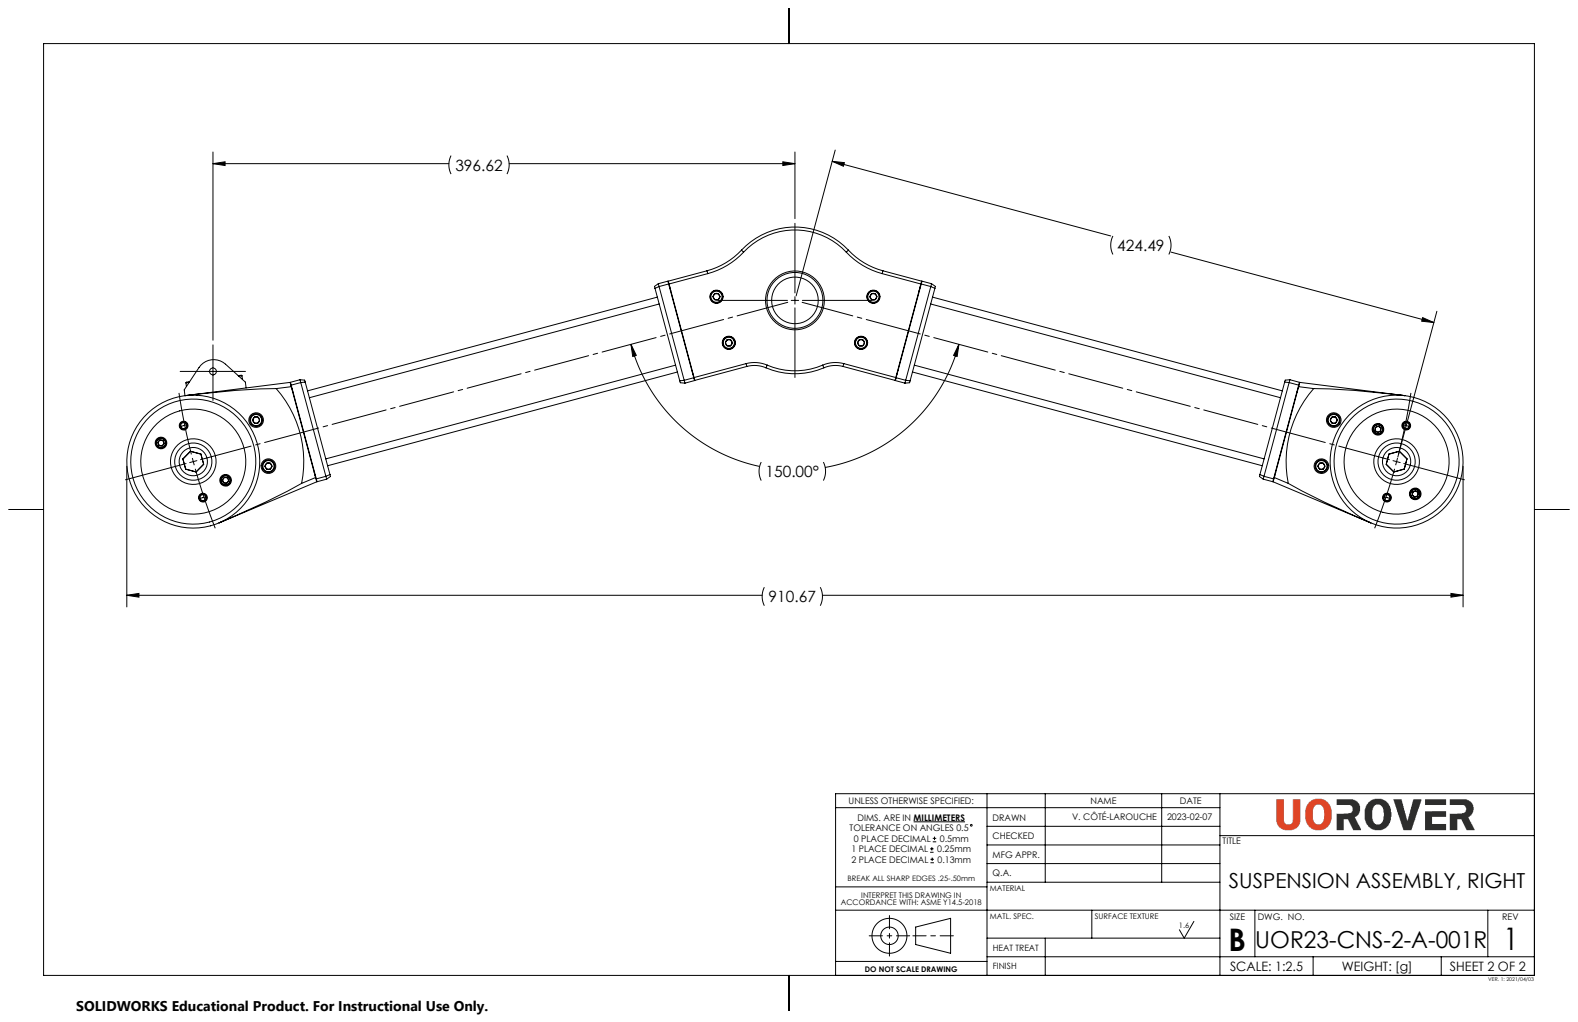
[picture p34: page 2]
SHEET 2 OF 2; SCALE: 1:2.5; WEIGHT: [g]; DWG. NO.; REV; V. CÔTÉ-LAROUCHE; HEAT TREAT; MATL. SPEC.; SURFACE TEXTURE; VER. 1: 2021/04/03

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

DRAWN
CHECKED
MFG APPR.
SUSPENSION ASSEMBLY, RIGHT Q.A.

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

DO NOT SCALE DRAWING

SOLIDWORKS Educational Product. For Instructional Use Only.

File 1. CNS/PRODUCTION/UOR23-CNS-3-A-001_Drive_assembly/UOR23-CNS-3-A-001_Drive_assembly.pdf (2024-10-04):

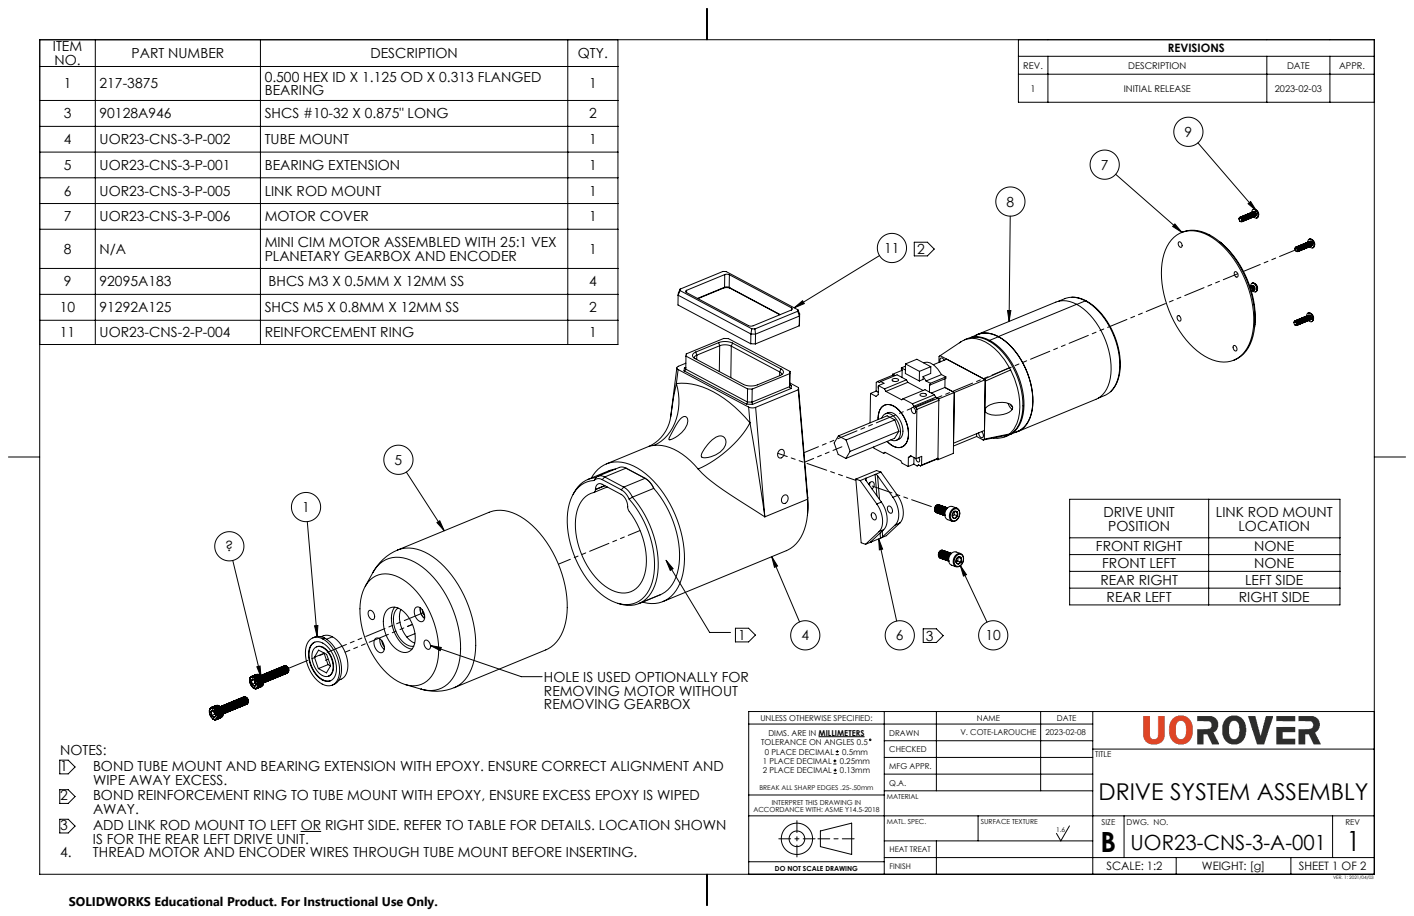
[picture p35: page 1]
BOND TUBE MOUNT AND BEARING EXTENSION WITH EPOXY. ENSURE CORRECT ALIGNMENT AND; BOND REINFORCEMENT RING TO TUBE MOUNT WITH EPOXY, ENSURE EXCESS EPOXY IS WIPED; ADD LINK ROD MOUNT TO LEFT OR RIGHT SIDE. REFER TO TABLE FOR DETAILS. LOCATION SHOWN; PART NUMBER; DESCRIPTION; QTY.; SHEET 1 OF 2; SCALE: 1:2; WEIGHT: [g]; DWG. NO.; REV; MFG APPR.; HEAT TREAT; MATL. SPEC.; SURFACE TEXTURE; VER. 1: 2021/04/03

1 | 217-3875 | 0.500 HEX ID X 1.125 OD X 0.313 FLANGED BEARING | 1

REV. | DESCRIPTION | DATE | APPR.
1 | INITIAL RELEASE | 2023-02-03

3 | 90128A946 | SHCS #10-32 X 0.875" LONG | 2
4 | UOR23-CNS-3-P-002 | TUBE MOUNT | 1
5 | UOR23-CNS-3-P-001 | BEARING EXTENSION | 1
6 | UOR23-CNS-3-P-005 | LINK ROD MOUNT | 1
7 | UOR23-CNS-3-P-006 | MOTOR COVER | 1
8 | N/A | MINI CIM MOTOR ASSEMBLED WITH 25:1 VEX PLANETARY GEARBOX AND ENCODER | 1

9 | 92095A183 | BHCS M3 X 0.5MM X 12MM SS | 4
10 | 91292A125 | SHCS M5 X 0.8MM X 12MM SS | 2
11 | UOR23-CNS-2-P-004 | REINFORCEMENT RING | 1

DRIVE UNIT POSITION | LINK ROD MOUNT LOCATION
FRONT RIGHT | NONE
FRONT LEFT | NONE
REAR RIGHT | LEFT SIDE
REAR LEFT | RIGHT SIDE

HOLE IS USED OPTIONALLY FOR
REMOVING MOTOR WITHOUT
REMOVING GEARBOX

UNLESS OTHERWISE SPECIFIED:
DIMS. ARE IN MILLIMETERS
TOLERANCE ON ANGLES 0.5
0 PLACE DECIMAL 0.5mm
1 PLACE DECIMAL 0.25mm
2 PLACE DECIMAL 0.13mm

V. COTE-LAROUCHE
DRIVE SYSTEM ASSEMBLY Q.A.

NOTES:
WIPE AWAY EXCESS.
AWAY.
IS FOR THE REAR LEFT DRIVE UNIT.
4. THREAD MOTOR AND ENCODER WIRES THROUGH TUBE MOUNT BEFORE INSERTING.

BREAK ALL SHARP EDGES .25-.50mm
MATERIAL INTERPRET THIS DRAWING IN
ACCORDANCE WITH: ASME Y14.5-2018

DO NOT SCALE DRAWING

SOLIDWORKS Educational Product. For Instructional Use Only.

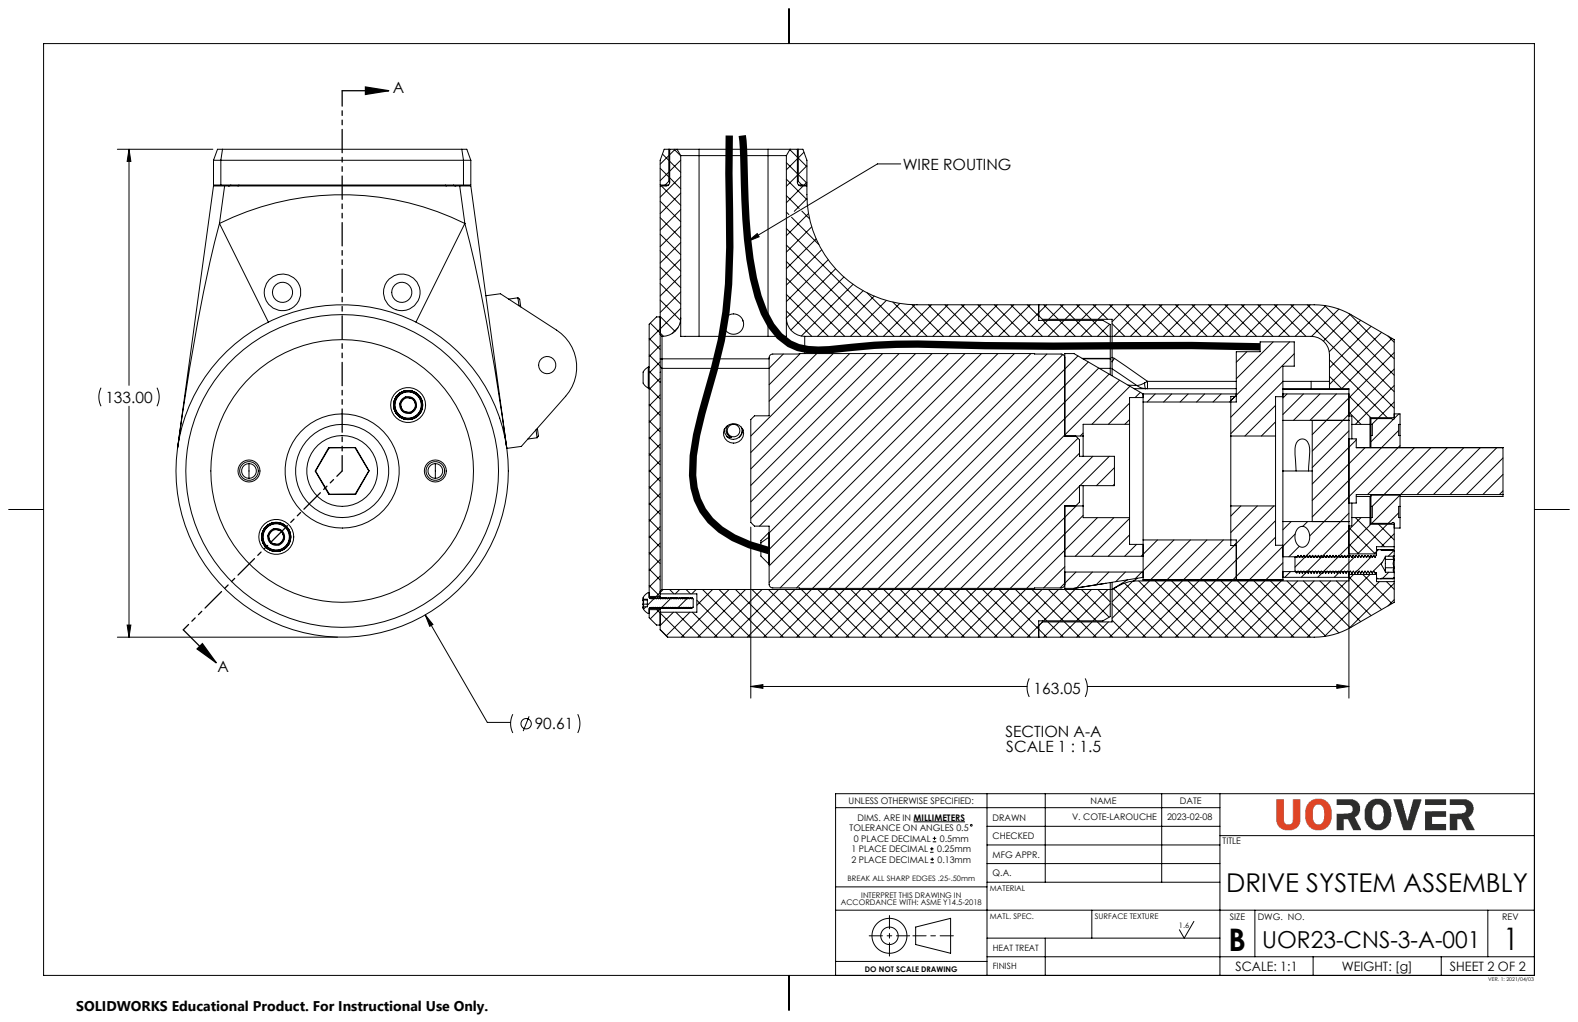
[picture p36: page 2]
SECTION A-A SCALE 1 : 1.5; WIRE ROUTING; SHEET 2 OF 2; SCALE: 1:1; WEIGHT: [g]; DWG. NO.; REV; MFG APPR.; HEAT TREAT; MATL. SPEC.; SURFACE TEXTURE; VER. 1: 2021/04/03

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

V. COTE-LAROUCHE
DRIVE SYSTEM ASSEMBLY Q.A.

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

DO NOT SCALE DRAWING

SOLIDWORKS Educational Product. For Instructional Use Only.

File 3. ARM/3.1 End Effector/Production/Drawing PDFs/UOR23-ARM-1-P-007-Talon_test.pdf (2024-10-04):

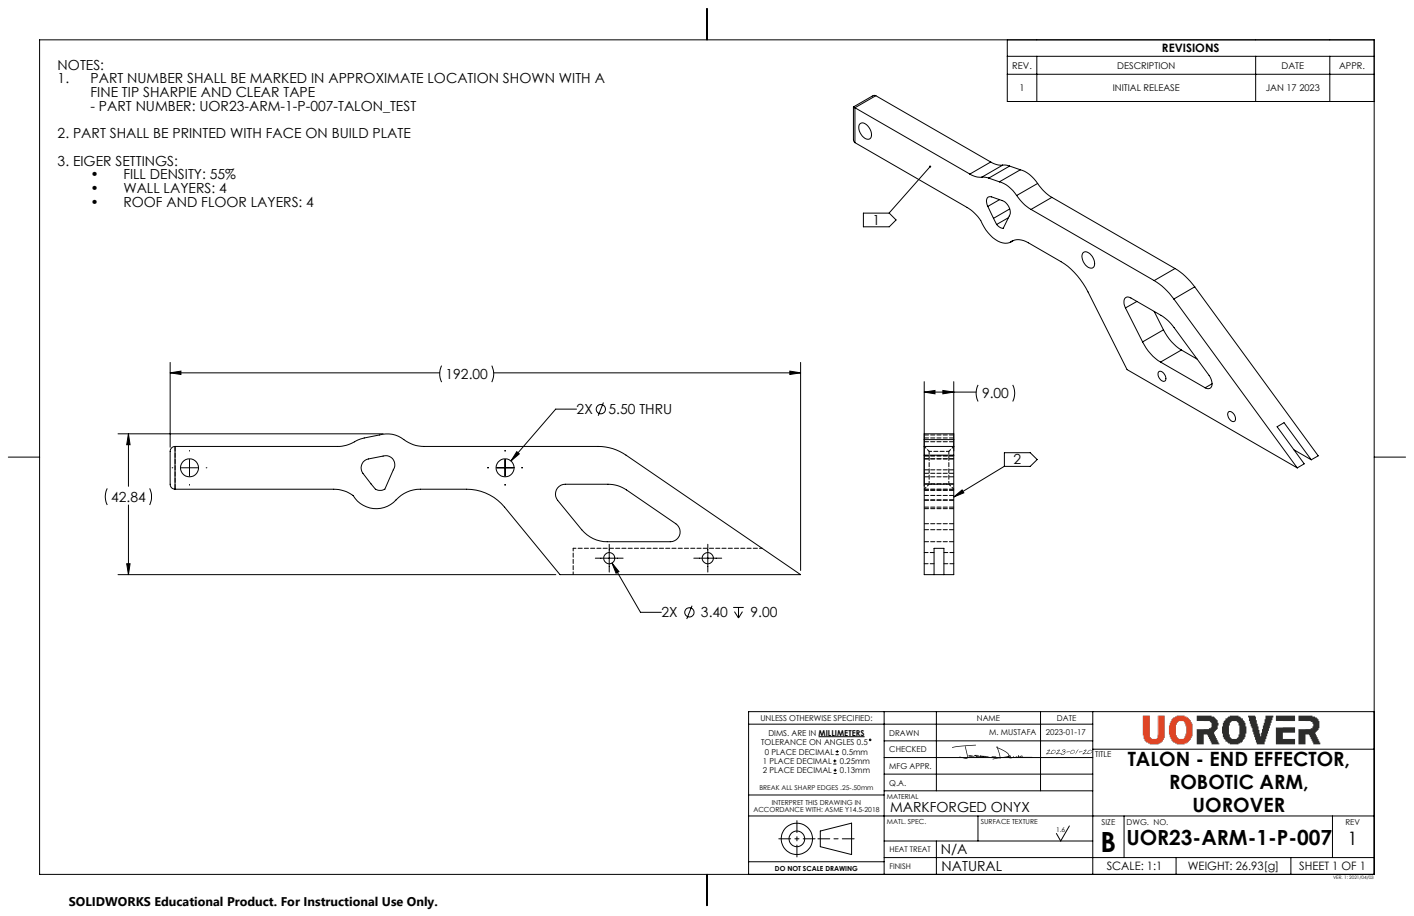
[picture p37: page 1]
2X 5.50 THRU; 3. EIGER SETTINGS: •; FILL DENSITY: 55% •; WALL LAYERS: 4 •; ROOF AND FLOOR LAYERS: 4; UOR23-ARM-1-P-007 1; MARKFORGED ONYX; DO NOT SCALE DRAWING; SHEET 1 OF 1; SCALE: 1:1; WEIGHT: 26.93[g]; DWG. NO.; REV; MFG APPR.; M. MUSTAFA; HEAT TREAT; MATL. SPEC.; SURFACE TEXTURE; VER. 1: 2021/04/03; TALON - END EFFECTOR, ROBOTIC ARM,

NOTES:
1. PART NUMBER SHALL BE MARKED IN APPROXIMATE LOCATION SHOWN WITH A
FINE TIP SHARPIE AND CLEAR TAPE
- PART NUMBER: UOR23-ARM-1-P-007-TALON_TEST
2. PART SHALL BE PRINTED WITH FACE ON BUILD PLATE

REV. | DESCRIPTION | DATE | APPR.
1 | INITIAL RELEASE | JAN 17 2023

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

SOLIDWORKS Educational Product. For Instructional Use Only.

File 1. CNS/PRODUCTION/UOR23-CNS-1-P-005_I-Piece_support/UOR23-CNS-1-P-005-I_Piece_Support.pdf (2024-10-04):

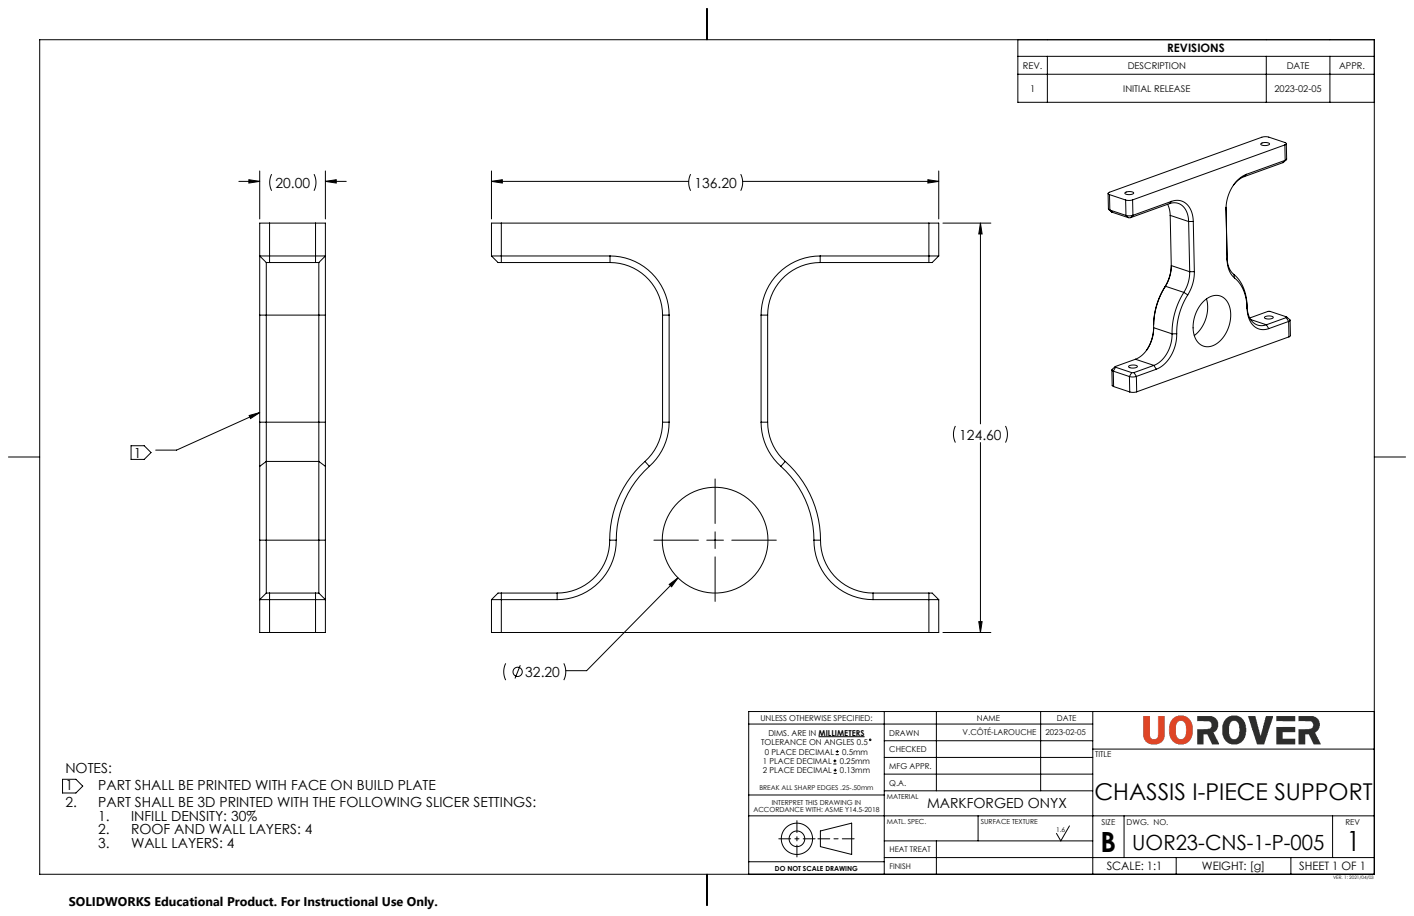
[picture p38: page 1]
PART SHALL BE PRINTED WITH FACE ON BUILD PLATE; SHEET 1 OF 1; SCALE: 1:1; WEIGHT: [g]; DWG. NO.; REV; MFG APPR.; HEAT TREAT; MATL. SPEC.; SURFACE TEXTURE; VER. 1: 2021/04/03

REV. | DESCRIPTION | DATE | APPR.
1 | INITIAL RELEASE | 2023-02-05

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

V.CÔTÉ-LAROUCHE
CHASSIS I-PIECE SUPPORT Q.A.
MARKFORGED ONYX

NOTES:
2. PART SHALL BE 3D PRINTED WITH THE FOLLOWING SLICER SETTINGS:
1. INFILL DENSITY: 30%
2. ROOF AND WALL LAYERS: 4
3. WALL LAYERS: 4

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

DO NOT SCALE DRAWING

SOLIDWORKS Educational Product. For Instructional Use Only.

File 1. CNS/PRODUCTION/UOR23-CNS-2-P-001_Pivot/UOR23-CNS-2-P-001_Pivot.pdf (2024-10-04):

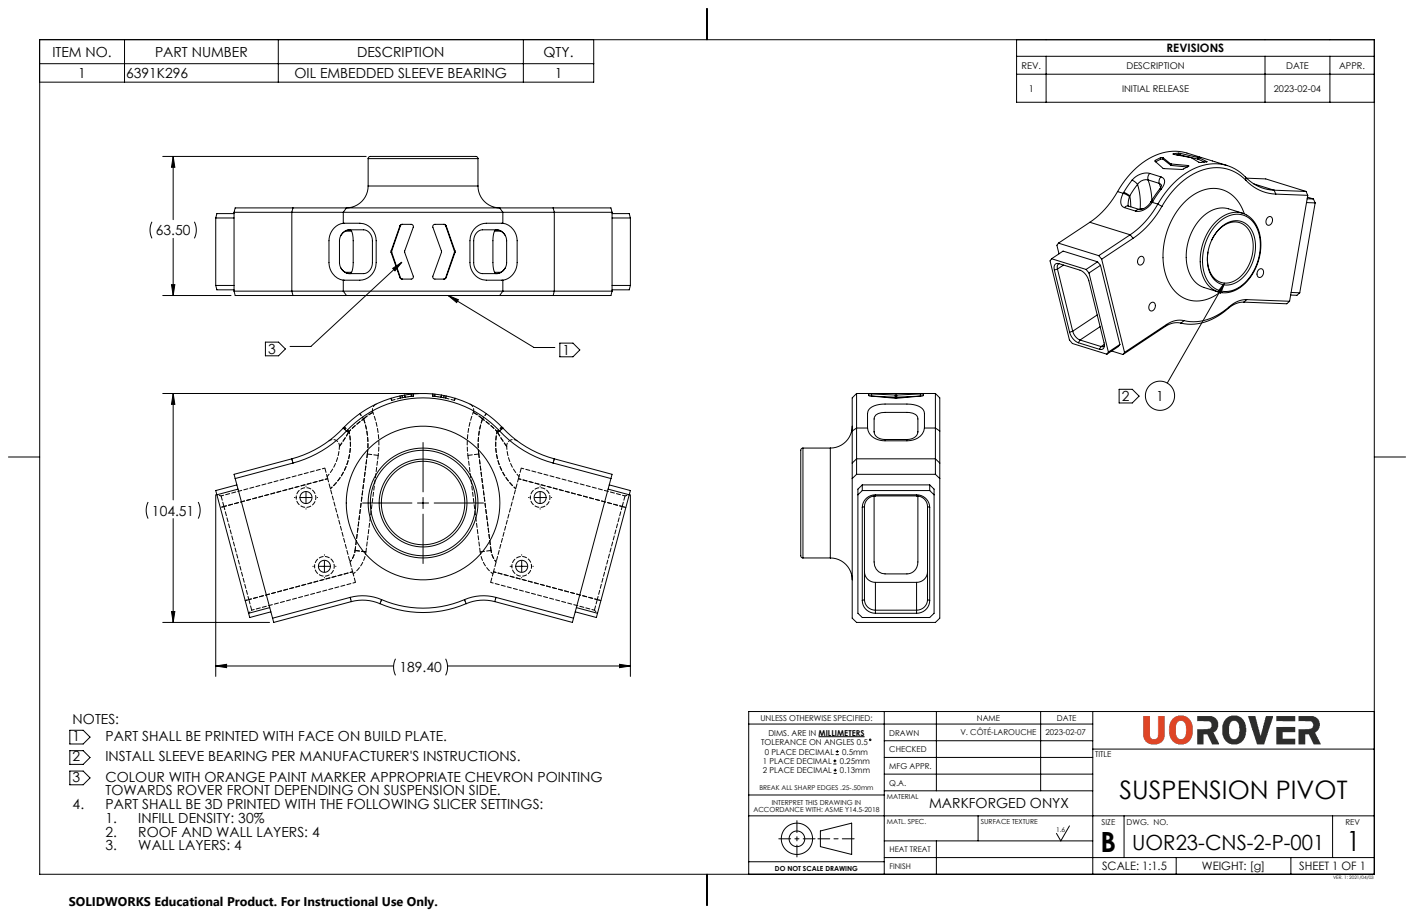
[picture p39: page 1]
PART SHALL BE PRINTED WITH FACE ON BUILD PLATE.; INSTALL SLEEVE BEARING PER MANUFACTURER'S INSTRUCTIONS.; COLOUR WITH ORANGE PAINT MARKER APPROPRIATE CHEVRON POINTING; MARKFORGED ONYX; ITEM NO.; PART NUMBER; DESCRIPTION; QTY.; OIL EMBEDDED SLEEVE BEARING; SHEET 1 OF 1; SCALE: 1:1.5; WEIGHT: [g]; DWG. NO.; REV; MFG APPR.; V. CÔTÉ-LAROUCHE; HEAT TREAT; MATL. SPEC.; SURFACE TEXTURE; SUSPENSION PIVOT Q.A.; VER. 1: 2021/04/03

REV. | DESCRIPTION | DATE | APPR.
1 | INITIAL RELEASE | 2023-02-04

NOTES:
TOWARDS ROVER FRONT DEPENDING ON SUSPENSION SIDE.
4. PART SHALL BE 3D PRINTED WITH THE FOLLOWING SLICER SETTINGS:
1. INFILL DENSITY: 30%
2. ROOF AND WALL LAYERS: 4
3. WALL LAYERS: 4

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

DO NOT SCALE DRAWING

SOLIDWORKS Educational Product. For Instructional Use Only.

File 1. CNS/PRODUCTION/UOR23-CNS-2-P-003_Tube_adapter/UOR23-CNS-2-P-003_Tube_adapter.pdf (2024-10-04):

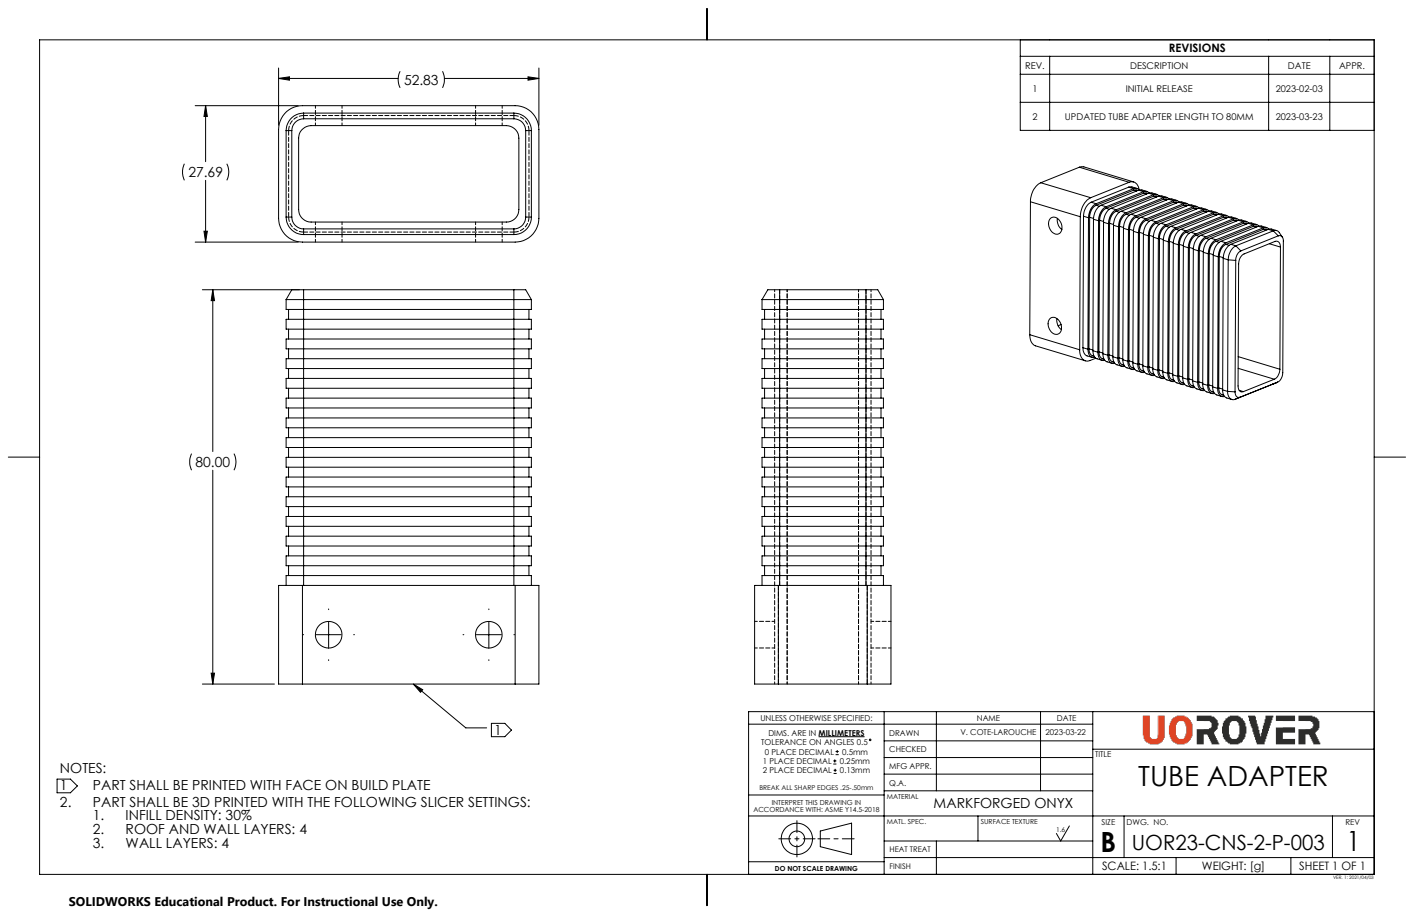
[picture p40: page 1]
PART SHALL BE PRINTED WITH FACE ON BUILD PLATE; SHEET 1 OF 1; SCALE: 1.5:1; WEIGHT: [g]; DWG. NO.; REV; MFG APPR.; V. COTE-LAROUCHE; HEAT TREAT; MATL. SPEC.; SURFACE TEXTURE; TUBE ADAPTER; VER. 1: 2021/04/03; MARKFORGED ONYX

REV. | DESCRIPTION | DATE | APPR.
1 | INITIAL RELEASE | 2023-02-03

2 | UPDATED TUBE ADAPTER LENGTH TO 80MM | 2023-03-23

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

DO NOT SCALE DRAWING

SOLIDWORKS Educational Product. For Instructional Use Only.

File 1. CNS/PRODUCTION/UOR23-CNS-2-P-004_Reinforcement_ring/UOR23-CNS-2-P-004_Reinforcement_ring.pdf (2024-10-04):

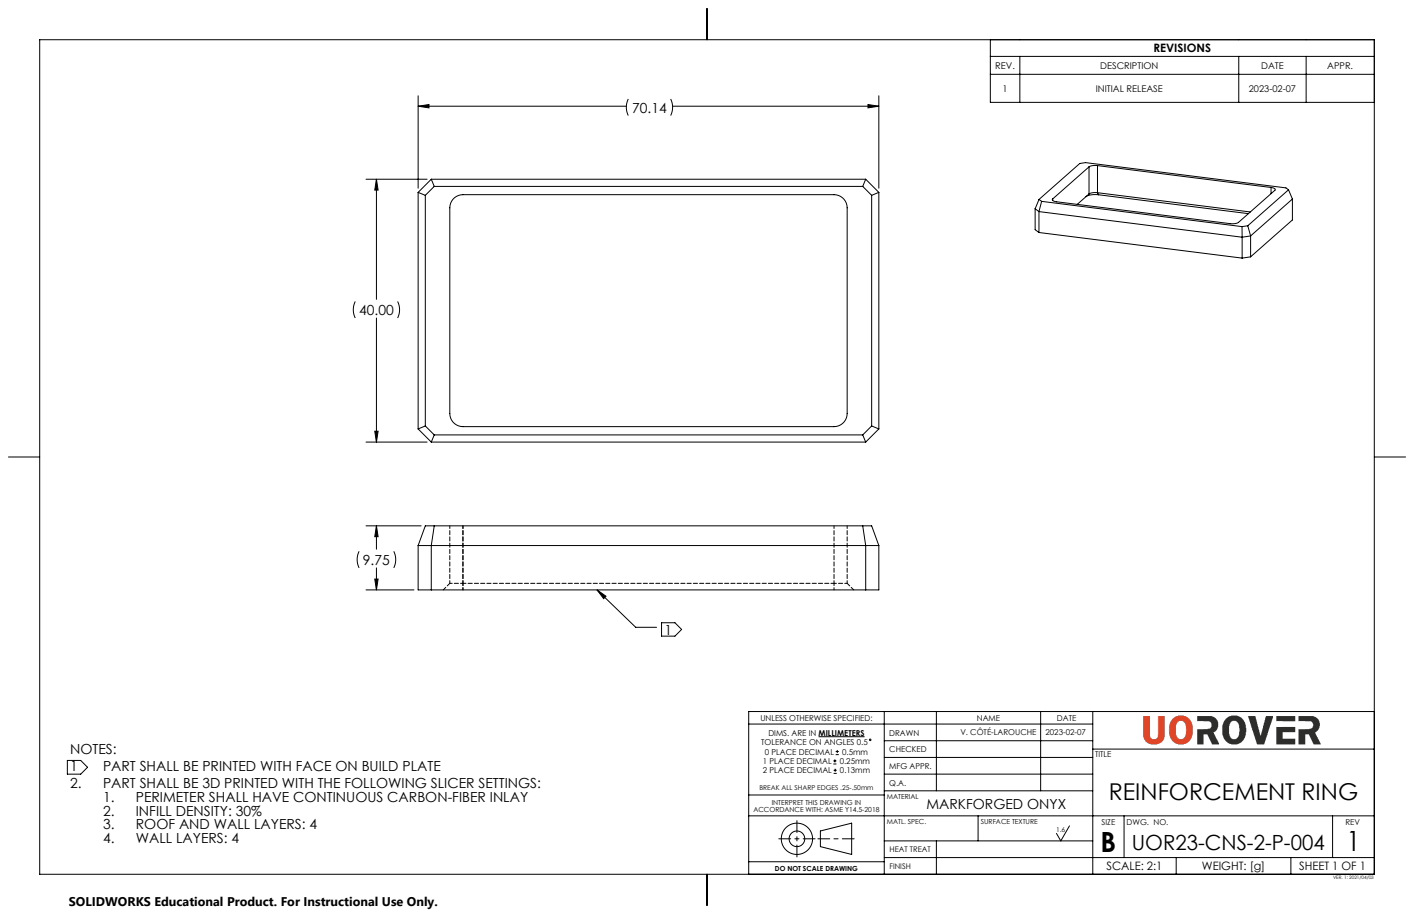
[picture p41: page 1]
PART SHALL BE PRINTED WITH FACE ON BUILD PLATE; MARKFORGED ONYX; SHEET 1 OF 1; SCALE: 2:1; WEIGHT: [g]; DWG. NO.; REV; MFG APPR.; V. CÔTÉ-LAROUCHE; HEAT TREAT; MATL. SPEC.; SURFACE TEXTURE; REINFORCEMENT RING Q.A.; VER. 1: 2021/04/03

REV. | DESCRIPTION | DATE | APPR.
1 | INITIAL RELEASE | 2023-02-07

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

NOTES:
2. PART SHALL BE 3D PRINTED WITH THE FOLLOWING SLICER SETTINGS:
1. PERIMETER SHALL HAVE CONTINUOUS CARBON-FIBER INLAY
2. INFILL DENSITY: 30%
3. ROOF AND WALL LAYERS: 4
4. WALL LAYERS: 4

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

DO NOT SCALE DRAWING

SOLIDWORKS Educational Product. For Instructional Use Only.

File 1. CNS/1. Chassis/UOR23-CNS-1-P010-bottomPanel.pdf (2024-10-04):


SOLIDWORKS Educational Product. For Instructional Use Only.
